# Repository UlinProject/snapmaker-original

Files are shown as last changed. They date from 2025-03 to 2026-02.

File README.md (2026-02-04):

<div id="header" align="center">

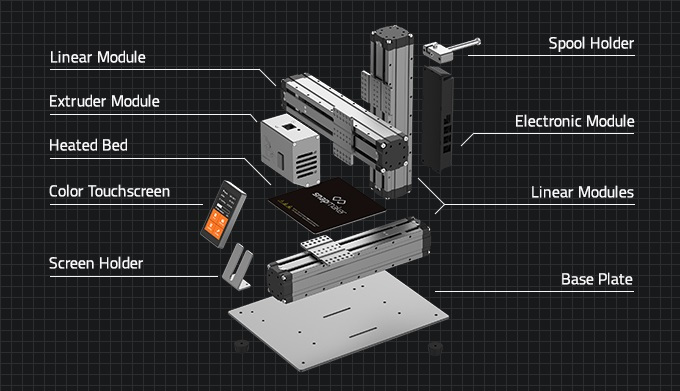
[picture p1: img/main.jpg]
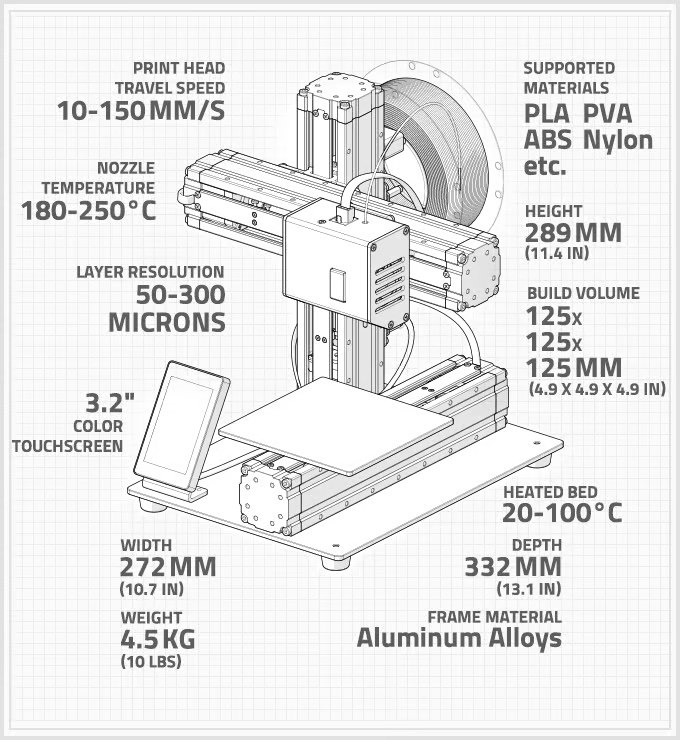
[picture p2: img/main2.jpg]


  <b>[snapmaker-original]</b>
  
  (Information about this 3D printer (Snapmaker original), set of modifications)
  </br></br>
<div id="badges">
  <a href="https://github.com/denisandroid">
    uproject
  </a>
</div>
</div>

## Description
I have been developing devices similar to 3D printers for a long time, I even created one self-assembling Cartesian printer based on a klipper (stm32f407, rails, belts) practically from scratch and one fine day, while studying a local trading platform, I came across this small and interesting printer. Initially, I was not interested in the quality of its 3D printing (I thought that if it prints, then it is already good), and I was only interested in its CNC capabilities and 3 in 1 technologies (3D, CNC, LASER).

My specific printer was manufactured in 2020-2021, and the printer model itself was first manufactured even earlier, around 2017-2018.

## Disclaimer
| :boom: Disclaimer |
|:------------------|
| :warning: Snapmaker is a registered trademark. The author has no affiliation with Snapmaker and does not provide hardware advice. For official support, please refer to the contacts listed on snapmaker. |
| :warning: Your actions and the information described here are entirely at your own risk. The author is not responsible for any damage to your devices. |
| :warning: All information provided is based on personal research and may contain errors. |
| :warning: This material is for informational purposes only. |

## Specifications

### Technique

#### Brain

| name | value |
| ---- | ----- |
| cpu | gd32f105rc6 (ARM; Flash: 256kB; 72-108MHz; external 16Mhz clock; SRAM: 96kB) |
| feedback | usb: ch340g (only 115200 baudrate, or 250000_baudrate/500000_baudrate in custom firmware, stable 921600 baudrate!) |
| power unit | 24V 5A (120w) |
| factory firmware | own firmware 2.11 based on marlin 1.1.0-RC6 (2016-04-24 12:00), gcode: marlin 1.1.0 + own set of instructions, licensed under <a href="https://www.gnu.org/licenses/gpl-3.0.ru.html">GPLv3</a> |
| firmware | ... <a href="./firmware/README.md">See all</a> |
| stepper motors | extruder Unknown 42HD4414-07 (1.8°(200), 2020/08/19) from mocotech, X Unknown 42HD4428-06 (1.8°(200), 2020/09/03) from mocotech, Y Unknown 42HD4428-06 (1.8°(200), 2020/09/03) from mocotech, Z Unknown 42HD4428-06 (1.8°(200), 2020/09/03) from mocotech ... <a href="./mods/BrainVoltageMod.md">See BrainVoltageMod</a> |
| drivers | extruder-rj45 (a4988, 16 steps, ~0.44vref, ~0.56A), X (a4988, 16 steps, ~0.87vref, ~1A), Y (a4988, 16 steps, ~0.87vref, ~1A), Z1 (a4988, 16 steps, ~0.87vref, ~1A), Z2 (X (a4988, 16 steps, ~0.87vref, ~1A)|

About factory firmware: The processor's performance fully covers the printer's capabilities, but the feedback significantly limits it due to the standard data transfer rate of 115200 baud. This is the first printer I know that prints better from a USB flash drive.

#### Factory Firmware Values and Limitations

| name | value |
| ---- | ----- |
| steps per unit | X 400.00, Y 400.00, Z400.00, E92.60 |
| microsteps | 16 |
| maximum feedrates (mm/s) | X 300.00, Y 300.00, Z 5.00, E 25.00 |
| 3d maximum acceleration (mm/s2) | X 1000, Y 1000, Z 100, E 10000 |
| cnc maximum acceleration (mm/s2) | X 100, Y 100, Z 100, E 100 |
| laser maximum acceleration (mm/s2) | X 3600, Y 3600, Z 3600 |
| accelerations printing | 1000.00 |
| accelerations retract | 1000.00 |
| accelerations travel| 1000.00 |
| min feedrate (mm/s) | S0 |
| min travel feedrate (mm/s) | T0 |
| minimum segment time (ms) | B20000 |
| maximum XY jerk (mm/s) | X20.00 |
| maximum Z jerk (mm/s) | Z0.40 |
| maximum E jerk (mm/s) | E5.00 |
| 3d work area | 125x125x125 mm |
| laser work area | 125x125 mm |
| cnc work area | 90x90x50 mm |

The printer manufacturer recommends a default head movement speed of 100 mm/s during printing, and a print speed of 40/50/60 mm/s and a retraction speed of 60 mm/s (at a distance of 5 mm).

The printer has one bad feature in the factory firmware, namely if you forgot to move the carriage home after printing, and it is in the maximum position (and after printing it is always in the maximum position), then after turning the printer off and on and pressing the home button, you will get a short-term impact of the head on the Z-axis limiter. The impact itself on the Z-axis limiter is not very critical, but very unpleasant and can lead to self-unscrewing.

### Physical
A thick aluminum plate on which the modular guides are located. The modular guides are based on a stepper motor + rigid coupling + four-way trapezoidal shaft, on top of the guide there is a thin aluminum plate with a conventional limit switch. The guides used are absolutely identical to the guides along the X, Y, Z axes, the order of connection to the motherboard determines the belonging of the guide to the desired axis. The moving carriage is held by openbuilds rollers.

<b>An anti-play system is present on each axle; the anti-play system operates on the basis of a classic spring.</b>
<b>If you are planning to modify the axes, I recommend starting with the Z-axis thrust bearing (F5-12M 5x12x4), as this is a high-load axis.</b>

#### Accuracy
The design features of the printer and the trapezoid shaft in the guides in combination with the "oak" a4988 should have shown good results, the manufacturer himself assures the accuracy of 50-300 microns. I calibrate each thread for accuracy and enter the data into the slicer, measuring with a caliper with a resolution of 0.01 mm and an error of 0.02 mm. In general, I get:

| NAME | PETG (default firmware)  | PLA (default firmware)  | PLA(klipper firmware +pa+is) |
| --- | --- | --- | --- |
| min absolute deviation (X and Y axes) | ~0.02mm | ~0.02mm | ~0.01mm |
| average absolute deviation (X and Y axes) | ~0.08mm | ~0.12mm | ~0.07mm |
| max absolute deviation (X and Y axes) | ~0.17mm | ~0.20mm | ~0.09mm |

In general, I have summarized many results of different filaments under the general one and described the general deviation of the two axes. I would also like to note that this printer gives more accurate results on the X-axis than on the Y-axis.

<b>The section is not finished yet.</b>

#### Cooling
Almost all of them use 24V fans, connected directly to 24V, i.e. they are uncontrollable. All fans are absolutely tiny and create a lot of noise, the saddest thing is that they are not very productive and I once managed to catch a traffic jam in the extruder due to not very good weather conditions.

It is recommended to replace almost all fans with larger ones.

#### Display
A very good solution, you can just take it as a phone and control the printer, a display with good resolution and more or less high-quality color gamut, not requiring a stylus. The solution is a ready-made purchased uart solution with its own microcontroller and program. The display is poorly compatible with the standard gcode for text displays and, for example, does not allow much under octoprint. I repeat that this display does not receive an image from the main microcontroller, but is independent.

### 3 In one

#### Extruder (3D)
A classic extruder built on the basis of an unknown to me full-size nemo 17 (1.8°(200), 42HD4414-07, 2020/08/19) from mocotech and gears (1:1, factory e-steps 92.60), a radiator noticeably larger than its classic versions, a convenient unknown to me thermal barrier, which involves fastening by screwing in one countersunk screw. By selection, it was established that the heating block itself is E3D V5, but with an unknown to me thermal barrier, which does not imply unscrewing from the block.

##### Bad design #1 (3D)
Instead of a capsule thermistor, a "droplet" type is used; the sensor itself is simply suspended inside the heating block and can move freely within it.

##### Bad design #2 (3D)
The manufacturer has provided a way to easily remove the cover and unscrew the fuser unit, but the rigid heating wires make it somewhat difficult to remove. Furthermore, if the "plastic plug" accidentally gets into the extruder during printing, the entire print head must be disassembled, a very time-consuming and tedious task.

##### Bad design #3 (3D)
The heating block itself is not insulated and, combined with an ineffective PID controller, the temperature fluctuates constantly.

##### Bad design #4 (3D)
While twisted pair cable is certainly an interesting and attractive solution when combined with a classic RJ45 connector, the cable cross-section from the "brain" to the extruder head proved unsatisfactory. Significant heating was observed, and the cable at best delivers 1.49 A with a voltage drop of 1.5 V (using an extruder with an output power of ~40 W will only deliver ~35 W, and even then, the resistance will fluctuate as the heater heats up. Using more powerful heaters of 50-60-80 W is impossible. Switching to an external MOSFET with a higher-quality cable resulted in a voltage drop of 0.1-0.2 V and an output power of approximately ~38 W using the same heater block, as well as the possibility of using more powerful extruders).

#### Bed (3D)
The textolite is small in size (128x128 mm), heating is exclusively resistive (24V, did not determine the power), heating up to 60-65 degrees is preferable (It is believed that temperatures above 80 degrees can damage the sticker coating). The main disadvantage of this table is the lack of insulation and all the heat is directed both to the platform itself and to heating its base (guide). Also, the bolts for fastening the platform to the guide are slightly larger than required, because of this, the screws themselves cut into the sticker glued to the platform a little (it is recommended to simply add a washer between the screw and the carriage, and then the screw will never damage the coating.). Another plus is that this sticker does not require any glue at all when printing PLA / PETG.

The first layer is calibrated in the printer very poorly, the calibration of the first layer is more truthful only at the moments of full heating of the platform, which the manufacturer did not provide for in the firmware. After calibrating the surface, you can more clearly evaluate the first layer on the model https://www.thingiverse.com/thing:3797458 (I am not the author of this model, it is simply in the public domain, <a href="https://creativecommons.org/licenses/by-nc/4.0/">Creative Commons - Attribution - Non-Commercial license</a>), and then perform the final calibration based on the model.

#### Spindle (CNC)
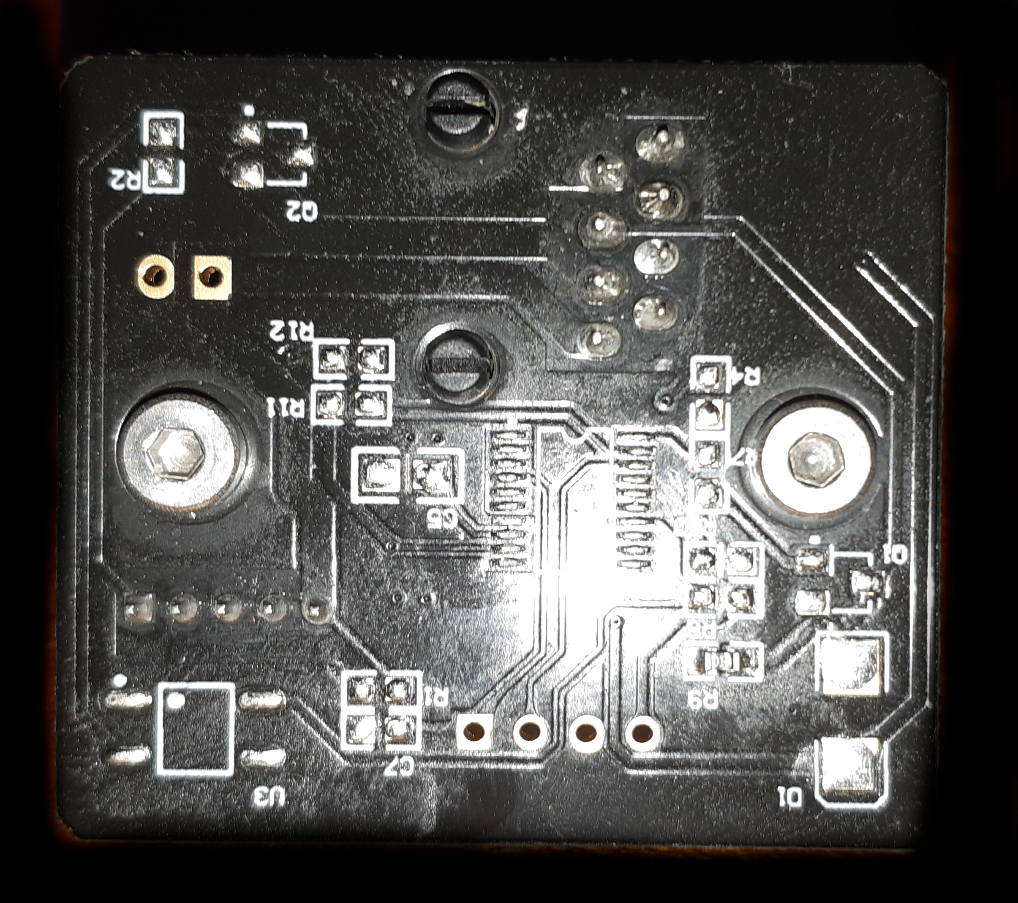
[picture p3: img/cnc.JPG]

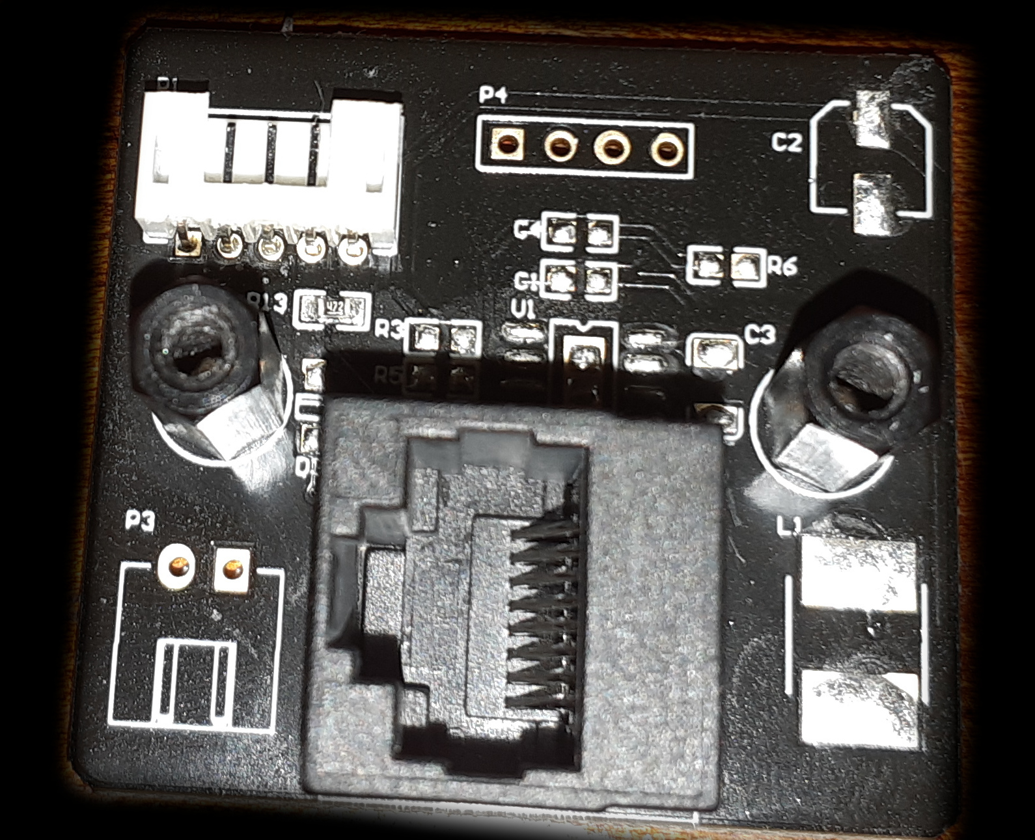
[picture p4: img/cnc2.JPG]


Uses a weak spindle 30W RBI-365024 24V, the main software assumes the use and configuration of specific cutters, the ability to perform drilling was not found. There are many shortcomings, no automatic centering, no speed control, a lot of noise during operation. The spindle control board is supposedly designed for control, but in the copy that I had, the board actually consisted of two resistors that do not assume speed control, there is only on / off control, carried out by the main brain board.

Also one of the minuses - the fastening of cutters / drills is not very good.

The spindle itself consists of a BLDC DC motor, MOSFET transistors, and a 4931ET driver (the electronics are hidden inside the spindle). The following pins are used for connection: AR, FG, FR, PWM, GND, and VCC (interestingly, there is a thick layer of solder between the PWM and GND pins from the factory).

#### Laser
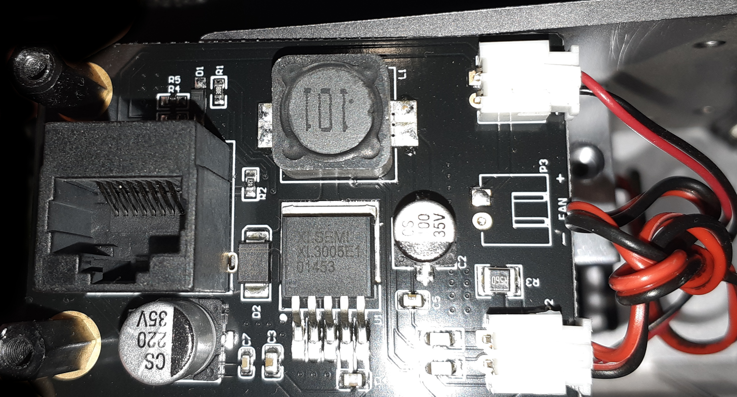
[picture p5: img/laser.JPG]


I have hardly used it and have not tested it. There is a dc/dc converter board inside and presumably the feedback and dc/dc regulation works. (will be added).

### Mods

#### Cooling of the thread (3D)
Cooling of the filament during printing is arranged in the strangest way, in general it is enough for someone, but for beginners I recommend printing and using https://www.thingiverse.com/thing:3403426 (I am not the author of this model, it is simply in the public domain, <a href="https://creativecommons.org/licenses/by/4.0/">Creative Commons - Attribution license</a>.)

#### Spool holder (3D)
<a href="./mods/SpoolHolder.md">See</a>

#### Thread Spool Holder (3D)
The thread holder allows you to correctly position the thread flow at a certain height, together with the modification of the holder, this is a comprehensive solution. Also, one of the advantages of this holder is that it allows you to easily move the engine control screen to the very top. https://www.thingiverse.com/thing:2757715 (I am not the author of this model, it is simply in the public domain, <a href="https://creativecommons.org/licenses/by/4.0/">Creative Commons - Attribution license</a>.)

#### Power unit
<a href="./mods/PowerUnit.md">See</a>

#### Strange Y-axis settings (settings for factory firmware only)
Initially, one oddity was noticed in the printer: if the X and Z axes were correctly limited by software and did not reach the limit, then the Y axis at the possible maximum slightly crashed into an obstacle. In general, this is not critical, since it crashed only one step and there is such a possibility that this is only me, but here is the fix:

```gcode
M1025 X131.00 Y128.00 Z128.00
M500
```
This g-code will determine the maximums for the axes and save the changes.

#### Brain cooling (cooling)
<a href="./mods/BrainCooling.md">See</a>

#### Octoprint (3D)
<a href="./mods/BrainCooling.md">See</a>

#### UART (feedback)
<a href="./mods/Uart.md">See</a>

#### Volcano (3D)
<a href="./mods/Volcano.md">See</a>

#### Gaps in the guides
The Y-guide design is not very good and involves large gaps through which debris can get in and affect the trapezoid screws; from time to time, various debris can get in there, including bolts or nuts (which, by the way, once happened to me), and especially considering that the manufacturer also assumes milling on this printer, the issue of debris is very acute.

There was a solution on the Internet using a paper accordion filter, which in theory can be made by yourself and the necessary parts can be printed for it https://www.thingiverse.com/thing:2828419 (I am not the author of this model, it is simply in the public domain, <a href="https://creativecommons.org/licenses/by-nc/4.0/">Creative Commons - Attribution - Non-Commercial license</a>.), at the moment I have not used this modification.

#### TMC2209? (stepper motor drivers)
In general, it would be possible to simply desolder the a4988 with a hair dryer and replace them with tmc2209, since they have similar pinout, and also change the harness a little and maybe even run the setup via uart and sensorless pointing, but at the moment I decided not to do this. The reason for using tmc2209 is simple, it is the ability to greatly reduce the noise of the stepper motors, but the StealthChop algorithm can also cause problems with circular geometry, and because of the a4988, the stepper motors are very noisy even in standby mode.

#### Klipper (new firmware)
Yes, this printer and this motherboard can be updated with Klipper, you can find the firmware in the firmwares called Klipper, you can simply follow the instructions and update the firmware without using JTAG or other means, just drop the file on a flash drive. Future updates of Klipper can be just as easy, also you can revert to the factory firmware at any time or to any other firmware.

| name | version | mcu | rate |
| ---- | ----- | ----- | ----- |
| Klipper_6_2025Demo460800.Bin | 121 commands, v0.12.0-452-g75a10bfca-dirty-20250308_020116-r510 / gcc: (Arch Repository) 14.2.0 binutils: (GNU Binutils) 2.43) | GD32F105RC6 | uart 480600 baudrate |

<a href="./firmware/Klipper.md">See</a>

#### Resonance compensation (only for klipper firmware)
<a href="./resonances/Readme.md">See</a>

#### Cura (slicer)
<a href="./cura/Readme.md">See</a>

#### My configuration (2025)

| name | value |
| ---- | ----- |
| heat block | volcano Plated Copper with insulator (TriangleLab) |
| heater | 24V 40W (TriangleLab), factory power limitation for the wires is approximately ~35W |
| sensor | 104NT-4 R025H42G in the sleeve (TriangleLab) |
| nozzle | E3D Volcano 0.4 (TriangleLab) |
| thermal barrier | unknown (the factory hole diameter was used, the thread was cut without additional drilling, and the heat break was simply selected and is unknown to me (the modifications to the heatsink suggest compatibility with factory heat breaks)). |
| lighting | ws2812b ribbon (5V, RP2040) |
| fan | 50mmX50mm 12V extruder (always on), DEFAULT CONFIGURATION |
| extruder | default Unknown 42HD4414-07 (~0.5A), MK8 (30 TEETH) |
| firmware | brain: klipper (v0.12.0, UART 921600baudrate), rp2040: klipper (v0.12.0, USB) |

#### My configuration (2026)

| name | value |
| ---- | ----- |
| heat block | volcano Plated Copper with insulator (TriangleLab) |
| heater | 24V 40W (TriangleLab), external MOSFET LR7843+new_wiring (support: 40,50,60,80..~120W) |
| sensor | 104NT-4 R025H42G in the sleeve (TriangleLab) |
| nozzle | E3D Volcano 0.4 (TriangleLab) |
| thermal barrier | titanium V6 (TriangleLab) (the heatsink was drilled out to a new, larger diameter, a new thread was cut, and an additional hole was made in the heatsink for installing another mounting screw for the heat break.) |
| wiring | general protection of all grounded wires, general grounding |
| lighting | ws2812b ribbon (5V, RP2040) |
| fan | 50x50mm 12V cooling extruder (only ON/OFF, always enabled by default if there is no control from the MCU, dc-dc LM2596S, PCA9685+LinuxMcu), default print_fan 24V (PWM 0-100%, module mosfet LR7843, PCA9685+LinuxMcu), 80x80mm 5V power unit (only ON/OFF, always enabled by default if there is no control from the MCU, dc-dc LM2596S, PCA9685+LinuxMcu+DS18B20), 80x80mm brain 5V cooling fan (PWM 0-100%, module mosfet LR7843, PCA9685+LinuxMcu+GD32F105InternalADCSensor)|
| extruder | new 17HS4401S (0.9°, configured ~1.34А), MK8 (50 TEETH) + THRUST BEARING (F5-12M 5x12x4) |
| axis | modified with thrust (F5-12M 5x12x4) bearing, new graphite screw nuts (T8x2x8, all axles) |
| firmware | klipper (v0.13.0, UART 460800baudrate), rp2040: klipper (v0.13.0, USB), linux_mcu: klipper (v0.13.0, internal process) |

## General impressions
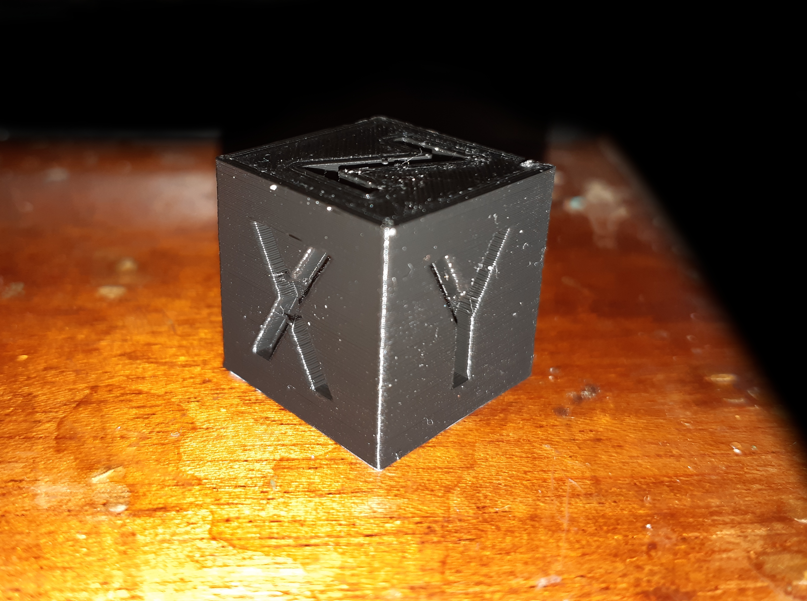
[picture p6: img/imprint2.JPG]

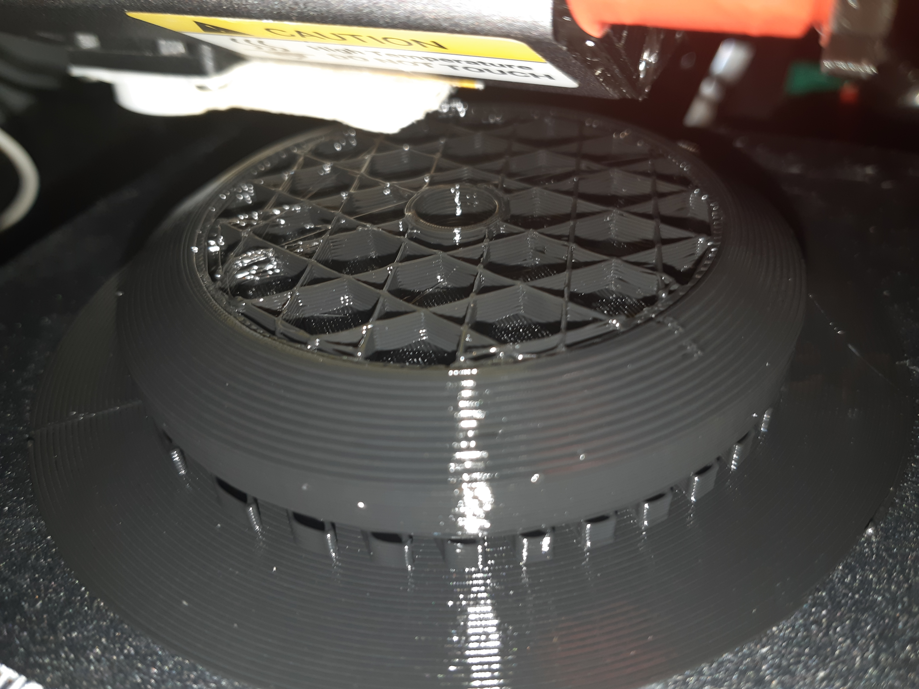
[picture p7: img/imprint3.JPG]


I liked the printer first of all for its assembly, it is completely aluminum, there are very few plastic parts, the printer creators even used thread locks and the idea of 3 in one is very catchy, but it has a very strong drawback, namely NOISE, which can be reduced by modifying the fans and ultimately the drivers, spindle...

As for the price, it turned out that this printer did not cost me that much, since the authors cut it out of their line, but at the same time, if I needed 3D printing, I could have initially bought something similar fast on "klipper".

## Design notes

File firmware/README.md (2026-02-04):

## Disclaimer
The firmware presented here is provided as is, I am not responsible for your damaged devices. All information described here is solely my experience and can be both useful and harmful to the end user. You can reflash your printers only at your own risk. Damage to your device can occur at any stage of the end user's actions. All images and firmware presented here are the property of their authors.

Snapmaker is a registered trademark, to which I have no relation, you can always contact the official contacts listed on the website snapmaker.com. All rights reserved.

## Firmware

| name | value | mod_list | stable |
| ---- | ----- | ----- | ----- |
| 32Base-2_11Original.Bin | The latest current firmware from the manufacturer in 2019, downloaded from open sources. Licensed under <a href="https://www.gnu.org/licenses/gpl-3.0.en.html">GPLv3</a> | | + |
| 32Base_2_11_01Demo250000BOUD.Bin | The first experiment on modifying this firmware, testing the reflashing method. Licensed under <a href="https://www.gnu.org/licenses/gpl-3.0.en.html">GPLv3</a> | +uart 115200BAUDRATE -> 250000BAUDRATE; | +(only tests) |
| 32Base_2_11_02Demo500000BOUDAndAdvancedOK | Second experiment, 500000BAUDRATE and ADVANCED_OK tests. | +uart 115200BAUDRATE -> 500000BAUDRATE; +uart advanced_ok; | +(only tests) |
| 32Base_2_11_04Demo500000BOUDAndMoreSerialMods | Experimenting with using the recommended settings for OctoPrint. Licensed under <a href="https://www.gnu.org/licenses/gpl-3.0.en.html">GPLv3</a> | +uart 115200BAUDRATE -> 500000BAUDRATE; +uart advanced_ok; +fix: BLOCK_BUFFER_SIZE(8->64); +fix: BUFSIZE(8->32); +fix: RX_BUFFER_SIZE(512->2048); | +(only tests) |
| Klipper | <a href="./Klipper.md">See</a> | ... | +(only tests) |

## Is it possible to get a brick when flashing?
Very low probability, since you can flash any firmware at any time, also remember that I am not responsible for your actions, you can use these firmwares only at your own risk.

## Saving settings?
Any firmware change resets the default settings, constantly having to adjust the height of the card.

## How to reflash?
1. Copy any file and rename it to Update.Bin to a USB disk formatted in Fat32.
2. Turn off the printer and insert the USB disk into the USB port.
3. Turn on the printer. If the LED changes as below, the update is successful.
- The blue LED blinks slowly for about 5 seconds.
- Then the LED turns off for about 2 seconds.
- The LED starts blinking quickly.
4. The flashing process is complete.

## Machine resonances?
<a href="./../resonances/Readme.md">See</a>

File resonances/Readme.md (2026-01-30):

#### Resonance compensation (only for klipper firmware)

## Description
It seems that this is exactly what this printer lacked from the factory. The printer itself has very good indicators on the X axis from the factory, but with the Y axis, not everything is so good even according to accuracy tests, after this calibration, the printer accuracy has increased significantly and it became possible to increase the acceleration, as well as print at higher speeds. I do not recommend making such accelerations as recommended by autocalibration, start from the fact that the acceleration from the factory is 1500 (on printing) / 3000 (on the laser), you can use 3000/6000 on printing, and maybe more, but I do not recommend you to set 76800/61500 right away, this is too much, remember that due to the features of the printer (trapezoidal shafts) the printer is subject to strong friction, you can thus wear out this printer very quickly, and I also recommend that you lubricate it more often.

<b>Please note that polyoxymethylene (POM) nuts are officially considered lubrication-free; they operate on the dry lubrication principle, and lubrication will only increase dust adhesion. However, lubrication has been proven to reduce friction even on POM nuts, and I use specialized lubricants that reduce dust adhesion. Your choice should be based solely on your own needs.</b>

<details>
  <summary>## My results (2025, Demo01, standard configuration, X-(mzv, vibrations = 0.0%, smoothing ~= 0.017, max_accel <= 45000 mm/sec), Y-(3hump_ei, vibrations = 3.7%, smoothing ~= 0.050, max_accel <= 12600 mm/sec))</summary>
    
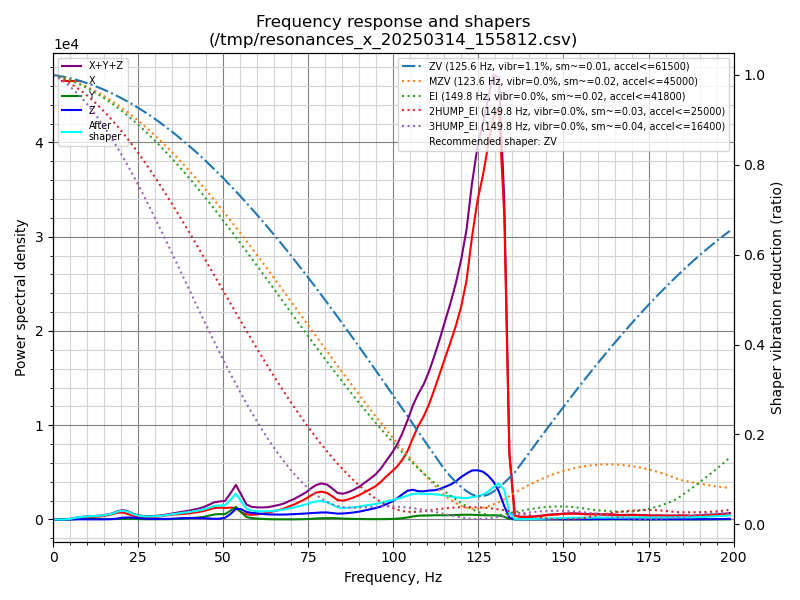
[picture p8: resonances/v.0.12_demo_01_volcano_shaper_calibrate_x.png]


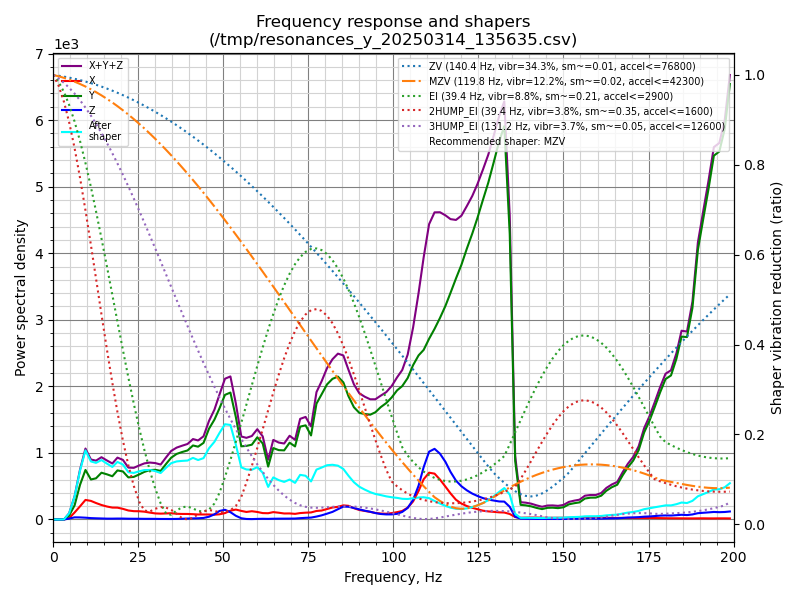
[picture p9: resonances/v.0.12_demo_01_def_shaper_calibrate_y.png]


X:
```
Fitted shaper 'zv' frequency = 125.6 Hz (vibrations = 1.1%, smoothing ~= 0.015)
To avoid too much smoothing with 'zv', suggested max_accel <= 61500 mm/sec^2
Fitted shaper 'ei' frequency = 149.8 Hz (vibrations = 0.0%, smoothing ~= 0.018)
To avoid too much smoothing with 'ei', suggested max_accel <= 41800 mm/sec^2
Fitted shaper '2hump_ei' frequency = 149.8 Hz (vibrations = 0.0%, smoothing ~= 0.028)
To avoid too much smoothing with '2hump_ei', suggested max_accel <= 25000 mm/sec^2
Fitted shaper '3hump_ei' frequency = 149.8 Hz (vibrations = 0.0%, smoothing ~= 0.040)
To avoid too much smoothing with '3hump_ei', suggested max_accel <= 16400 mm/sec^2
Fitted shaper 'mzv' frequency = 123.6 Hz (vibrations = 0.0%, smoothing ~= 0.017)
To avoid too much smoothing with 'mzv', suggested max_accel <= 45000 mm/sec
```

Y:
```
Fitted shaper 'zv' frequency = 140.4 Hz (vibrations = 34.3%, smoothing ~= 0.013)
To avoid too much smoothing with 'zv', suggested max_accel <= 76800 mm/sec^2
Fitted shaper 'mzv' frequency = 119.8 Hz (vibrations = 12.2%, smoothing ~= 0.018)
To avoid too much smoothing with 'mzv', suggested max_accel <= 42300 mm/sec^2
Fitted shaper 'ei' frequency = 39.4 Hz (vibrations = 8.8%, smoothing ~= 0.208)
To avoid too much smoothing with 'ei', suggested max_accel <= 2900 mm/sec^2
Fitted shaper '2hump_ei' frequency = 39.4 Hz (vibrations = 3.8%, smoothing ~= 0.348)
To avoid too much smoothing with '2hump_ei', suggested max_accel <= 1600 mm/sec^2
Fitted shaper '3hump_ei' frequency = 131.2 Hz (vibrations = 3.7%, smoothing ~= 0.050)
To avoid too much smoothing with '3hump_ei', suggested max_accel <= 12600 mm/sec
```

The results are more like the truth, but I'm not entirely sure about them, since these are the very first resonance measurements I made on this printer. The measurement was made directly on the nozzle itself, and on the heated platform at its very edge. What I can say is that the autocalibrator's choice of 1.1% vibrations is very strange, when you can choose 0%, but not at such high accelerations, and I also can't say with certainty that the chosen shaper will help 100%, since there are spikes at different frequencies.

## At the moment I am using this configuration (Demo01)

```toml
[input_shaper]
shaper_type_x: mzv
shaper_freq_x: 123.6
shaper_type_y: 3hump_ei
shaper_freq_y: 131.2
```

Yes, the Y axis is limited to a max of 12600 acceleration, but that seems to be the best the shaper can offer on that axis with minimal vibration.
  
</details>

<details open>
  <summary>## My results (2026, design changes, X-(mzv, vibrations = 0.0%, smoothing ~= 0.014, max_accel <= 49800 mm/sec), Y-(2hump_ei, vibrations = 1.0%, smoothing ~= 0.031, max_accel <= 20200 mm/sec))</summary>
    
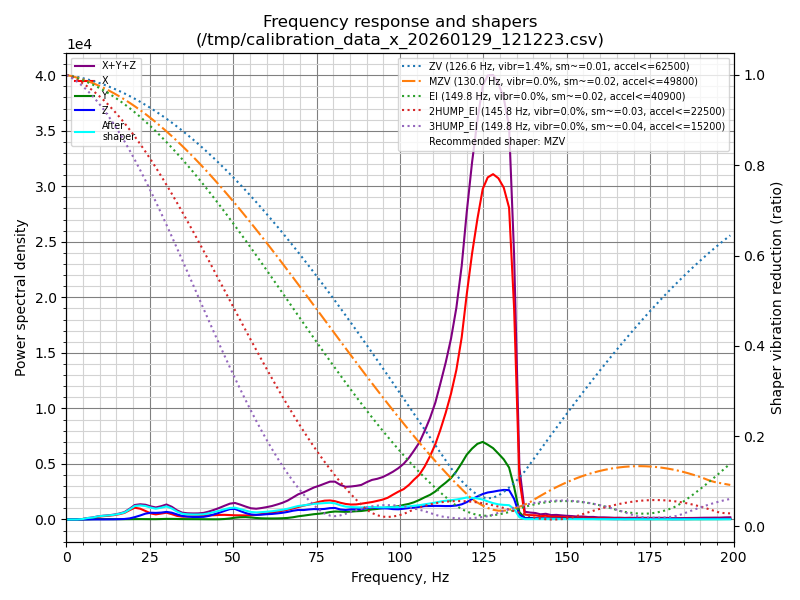
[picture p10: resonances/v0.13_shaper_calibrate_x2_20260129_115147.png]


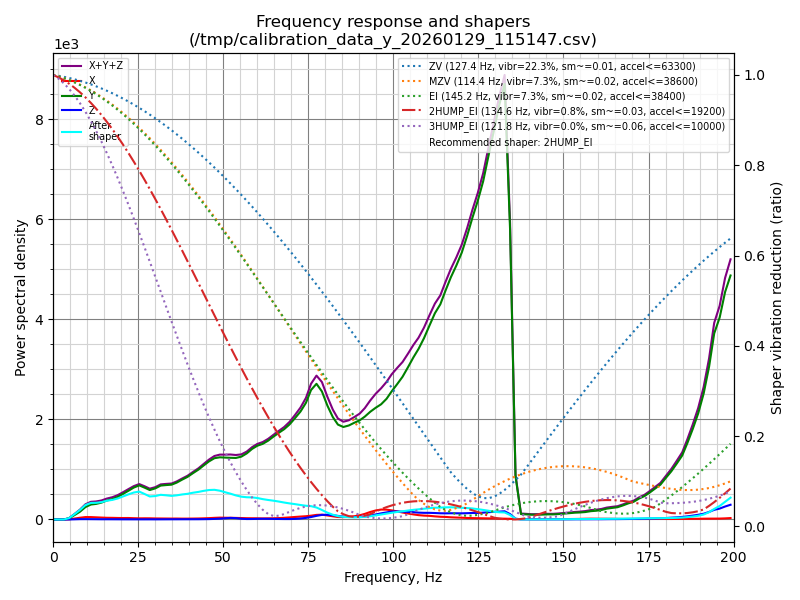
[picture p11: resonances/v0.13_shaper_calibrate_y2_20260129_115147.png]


X:
```
// Fitted shaper 'zv' frequency = 126.6 Hz (vibrations = 1.4%, smoothing ~= 0.013)1
// To avoid too much smoothing with 'zv', suggested max_accel <= 62500 mm/sec
// Fitted shaper 'mzv' frequency = 130.0 Hz (vibrations = 0.0%, smoothing ~= 0.014)
// To avoid too much smoothing with 'mzv', suggested max_accel <= 49800 mm/sec
// Fitted shaper 'ei' frequency = 149.8 Hz (vibrations = 0.0%, smoothing ~= 0.016)
// To avoid too much smoothing with 'ei', suggested max_accel <= 40900 mm/sec
// Fitted shaper '2hump_ei' frequency = 145.6 Hz (vibrations = 0.0%, smoothing ~= 0.028)
// To avoid too much smoothing with '2hump_ei', suggested max_accel <= 22500 mm/sec
// Fitted shaper '3hump_ei' frequency = 149.8 Hz (vibrations = 0.0%, smoothing ~= 0.040)
// To avoid too much smoothing with '3hump_ei', suggested max_accel <= 15200 mm/sec

// Recommended shaper_type_x = mzv, shaper_freq_x = 130.0 Hz
// shaper_type_x:mzv shaper_freq_x:130.000 damping_ratio_x:0.100000
// shaper_type_y:2hump_ei shaper_freq_y:138.200 damping_ratio_y:0.100000
// Shaper calibration data written to /tmp/calibration_data_x_20260129_121223.csv file
```

Y:
```
// Fitted shaper 'zv' frequency = 129.2 Hz (vibrations = 24.8%, smoothing ~= 0.013
// To avoid too much smoothing with 'zv', suggested max_accel <= 65100 mm/sec
// Fitted shaper 'mzv' frequency = 115.6 Hz (vibrations = 7.0%, smoothing ~= 0.017)
// To avoid too much smoothing with 'mzv', suggested max_accel <= 39400 mm/sec
// Fitted shaper 'ei' frequency = 149.8 Hz (vibrations = 7.9%, smoothing ~= 0.016)
// To avoid too much smoothing with 'ei', suggested max_accel <= 40900 mm/sec
// Fitted shaper '2hump_ei' frequency = 138.2 Hz (vibrations = 1.0%, smoothing ~= 0.031)
// To avoid too much smoothing with '2hump_ei', suggested max_accel <= 20200 mm/sec
// Fitted shaper '3hump_ei' frequency = 125.0 Hz (vibrations = 0.0%, smoothing ~= 0.057)
// To avoid too much smoothing with '3hump_ei', suggested max_accel <= 10600 mm/sec

// Recommended shaper_type_y = 2hump_ei, shaper_freq_y = 138.2 Hz
// shaper_type_x:mzv shaper_freq_x:123.600 damping_ratio_x:0.100000
// shaper_type_y:2hump_ei shaper_freq_y:138.200 damping_ratio_y:0.100000
// Shaper calibration data written to /tmp/calibration_data_y_20260129_115147.csv file
```

As paradoxical as it may sound, testing shows that after a year of active use, the printer has become even more rigid and can now handle even higher accelerations than before. But there's nothing unusual about it; I simply performed this second calibration after a complete teardown, high-quality lubrication, and the installation of new black POM nuts, along with my own modification—installing thrust bearings on the stepper motors (which only works effectively on the Z-axes).

```toml
[input_shaper]
shaper_type_x: mzv
shaper_freq_x: 130.0
shaper_type_y: 2hump_ei
shaper_freq_y: 138.2
```

</details>

## How to calibrate?
There are no special recommendations here, I recommend using the official documentation, I will simply tell you how I calibrated this printer. For starters, you can use any high-speed microcontroller, for example, rp2040/rp2350 with an adxl345 accelerometer, I simply used stm32f103 with an adxl345 accelerometer soldered in by myself and flashed it with the latest klipper firmware, one microcontroller with adxl is enough for separate calibration of one axis, and then another, just calibrate one axis and move the calibrator to the other, and then calibrate it too.

### Configuration example
Note the order of the X, Y, Z axes and determine in which axis order you install the accelerometer.
```toml
[mcu mcu2]
serial: /dev/serial/by-id/usb-Klipper_stm32f103xe_25002700010000343333574E-if00
restart_method: command

[adxl345 AXES_X_OR_Y]
cs_pin: mcu2:PA4
spi_speed: 5000000
# axes_map: y, x, z # Change only if you think it is necessary to ensure that the axes match.
spi_bus: spi1
rate: 3200

[resonance_tester]
accel_chip: adxl345 AXES_X_OR_Y
move_speed: 60
probe_points:
    62.5, 62.5, 20

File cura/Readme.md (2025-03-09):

#### Cura
In general, you can use Luban, it has good settings for this printer on the old Cura engine, but it has a simpler setup interface and in some places even more thought out than Cura, but very limited in functionality. Or a completely different slicer, but I adapted specifically Cura.

| name | value |
| ---- | ----- |
| X (width) | 125.0 |
| Y (width) | 125.0 |
| Z (height) | 125.0 |
| Build plate shape | Rectangler |
| Origin at center |  |
| Heated bed | + |
| Heated build volume |  |
| G-code flavor | Marlin |
| X min | -20 |
| Y min | -10 |
| X max | 10 |
| Y max | 10 |
| Gantry Height | 125.0 |
| Number of Extruders | 1 |
| Apply Extruder offsets to gcode | + |

Start G-code
```gcode
M1005

T0
M82 ;absolute extrusion mode
;Start GCode begin
M104 S{material_print_temperature_layer_0} ;Set Hotend Temperature
M140 S{material_bed_temperature_layer_0} ;Set Bed Temperature
G28 ;home
M400 ; WAIT END G0/G1
M109 S{material_print_temperature_layer_0} ;Wait for Hotend Temperature
M190 S{material_bed_temperature_layer_0} ;Wait for Bed Temperature
G90 ;absolute positioning
G0 X-10 Y-10 F3000
G0 Z0 F1800
G92 E0
G1 E25 F190 ; Extrusion
G92 E0

G0 X0 Y0 F3000 ;Move to origin
G0 Z1 F1800 ;Move up to avoid scraping against heated bed

;Start GCode end
```

End G-code
```gcode
M140 S0
M107
;End GCode begin
M400 ; WAIT END G0/G1
M104 S0 ;extruder heater off
M140 S0 ;heated bed heater off (if you have it)
G90 ;absolute positioning
G92 E0
G1 E-1 F300 ;retract the filament a bit before lifting the nozzle, to release some of the pressure
G1 Z125 E-1 F3000 ;move Z up a bit and retract filament even more
G1 X0 F3000 ;move X to min endstops, so the head is out of the way
G1 Y125 F3000 ;so the head is out of the way and Plate is moved forward
;End GCode end
M82 ;absolute extrusion mode
M104 S0
;End of Gcode
```

| name | value |
| ---- | ----- |
| Nozzle size | 0.4 |
| Compatible material diametr | 1.75 |
| Nozzle offset X | 0.0 |
| Nozzle offset Y | 0.0 |
| Cooling Fan Number | 0.0 |
| Extruder Start G-code duration | 0.0 |
| Extruder End G-code duration | 0.0 |

Next, I recommend installing `Cura-MaterialSettingsPlugin` or a similar plugin to distribute settings between the filament and the printer profile.

In the files I will attach a print profile adapted for this printer (but I have a "volcano") and an example of settings for one of the types of plastic.

<b>The section is not finished yet.</b>

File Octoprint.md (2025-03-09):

#### Octoprint


I have long been accustomed to the "klipper" and at the moment I wanted to keep the original brains, but at the same time have the ability to print and control the printer over the network, the simplest solution was to install an octoprint.

There are no special recommendations here, and some parameters may not suit you. (there may also be errors here)

| name | value |
| ---- | ----- |
| name | Snapmaker Original |
| model | Snapmaker Original |
| form factor | Rectangler |
| origin | Lower left |
| heated bed | + |
| width (X) | 125 |
| depth (Y) | 125 |
| height (Z) | 125 |
| axes X | 10000 |
| axes Y | 10000 |
| axes Z | 220 |
| axes E | 1000 |
| nozzle diameter | 0.4 |
| number of extruders | 1 |
| default extrusion length | 5 |

<b>Please note</b> that if you are using 500000 baud, this needs to be specified in the Octoprint alternative speeds, but if you are using 250000 baud, nothing like that is required.

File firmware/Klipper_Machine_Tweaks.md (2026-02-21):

### Klipper Machine Tweaks

#### # UART Interface
Use the built-in UART interface for direct MCU communication.

Documentation: <a href="../mods/Uart.md#direct-uart-connection-to-sbc-single-board-computer">See Uart.md</a>.

#### # USB (cmdline.txt)
Optimizations for the USB stack and CPU scheduling.

Path (add to the end): /boot/firmware/cmdline.txt
```
 dwc_otg.lpm_enable=0 dwc_otg.fiq_fsm_enable=1 dwc_otg.nak_holdoff=1
```
<b>dwc_otg:</b> Disables USB power management and optimizes interrupt handling to ensure stable MCU connection.

#### # USOLCPUS (cmdline.txt)
Dedicate one CPU core exclusively to running Klipper.

Path (add to the end): /boot/firmware/cmdline.txt
```
 isolcpus=3
```
<b>isolcpus=3:</b> Isolates the 4th CPU core from the Linux general scheduler for exclusive Klipper use.

##### Process Priority & CPU Affinity
Script: /bin/klipper_update_priority
```bash
#! /bin/bash
KLIPPER_PID=$(pgrep -f "klippy.py")

if [ -n "$KLIPPER_PID" ]; then
    chrt -f -p 40 $KLIPPER_PID       # Set Real-Time priority
    taskset -cp 3 $KLIPPER_PID       # Bind to isolated core 3
    ionice -c 1 -n 0 -p $KLIPPER_PID # Maximize I/O priority
fi
```
File: /etc/cron.d/klipper
```
@reboot root bash /bin/klipper_update_priority
*/5 * * * * root bash /bin/klipper_update_priority
```
File: /etc/default/irqbalance
```
IRQBALANCE_BANNED_CPUS=00000008
```

#### # System Performance (/etc/rc.local)

##### CPU Frequency

Script (add to the end): /etc/rc.local
```bash
cpupower frequency-set --min 1.2Ghz
cpupower frequency-set -g performance
```

##### Logging & Network
Script (add to the end): /etc/rc.local
```bash
mount -t tmpfs tmpfs /home/alarm/printer_data/logs/
iw dev wlan0 set power_save off
```

##### Extreme Real-Time Tuning
Note: Use with caution. Removes the 5% CPU safety margin for the OS.

Script (add to the end): /etc/rc.local
```bash
sysctl -w kernel.sched_rt_runtime_us=-1
```

##### CMA (if you don't use the display, rpi3 machine)
Note: Just free up some RAM by cutting cma. How much free space is in the CMA? Check with cat /proc/meminfo (usually free 28m).

Path (add to the end): /boot/firmware/cmdline.txt
```
 cma=32M
```

##### Mitigations + off_audit (be aware of the risks)
Path (add to the end): /boot/firmware/cmdline.txt
```
 mitigations=off audit=0
```

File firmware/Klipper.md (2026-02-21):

## Description
A full featured clipper port for this printer, allowing you to overclock and expand the capabilities ("pressure advance", "input shaper", "bl-touch", "nozzle cleaner", "fan control", ...) of this printer using a single board computer and other additional microcontrollers.

## Disclaimer
The firmware presented here is provided as is, I am not responsible for your damaged devices. All information described here is solely my experience and can be both useful and harmful to the end user. You can reflash your printers only at your own risk. Damage to your device can occur at any stage of the end user's actions. All images and firmware presented here are the property of their authors.

Snapmaker is a registered trademark, to which I have no relation, you can always contact the official contacts listed on the website snapmaker.com. All rights reserved.

## Firmware
| name | value | stable |
| ---- | ----- | ----- |
| Klipper_6_2025Demo460800.Bin | Experimental current (as of 2025) demo firmware klipper. Licensed under <a href="https://www.gnu.org/licenses/gpl-3.0.en.html">GPLv3</a> | +-(only tests) |
| Klipper_10_v0.12.0_2025.zip | Relevant for start 2025, functionality is not cut. Firmware in the archive, you need to unpack and select the desired baudrate, if you do not know the baudrate take 250000, ONLY UART (UART via USB or directly). Licensed under <a href="https://www.gnu.org/licenses/gpl-3.0.en.html">GPLv3</a> | +(only tests) |
| Klipper_12_v0.13.0_2025.zip | Relevant for 2025-2026, functionality is not cut. Firmware in the archive, you need to unpack and select the desired baudrate, if you do not know the baudrate take 250000, ONLY UART (UART via USB or directly). Licensed under <a href="https://www.gnu.org/licenses/gpl-3.0.en.html">GPLv3</a> | + |

## How to reflash?
1. Copy any file and rename it to Update.Bin to a USB disk formatted in Fat32.
2. Turn off the printer and insert the USB disk into the USB port.
3. Turn on the printer. If the LED changes as below, the update is successful.
- The blue LED blinks slowly for about 5 seconds.
- Then the LED turns off for about 2 seconds.
- The LED starts blinking quickly.
4. The flashing process is complete.

## Don't forget to remove the flash drive
The "klipper" firmware does not delete the "Update.Bin" file after flashing, so you can constantly reflash the device when you turn it on (even if you don't want to). It is better to either remove the flash drive or delete the "Update.Bin" file on it. In the Marlin firmware, this is done automatically.

## Is it possible to return to the factory firmware?
At any time, in the same way, by dropping the original Update.bin onto a flash drive.

## 921600/500000/460800/250000?
I can't give you a definitive answer, but this printer works fine at 500,000 baud and above. I currently use 921600 regularly, but Klipper officially recommends 250,000, and according to official statements, that should be enough, but the overall command throughput may be low.

<i>After switching to a detachable UART cable (previously, it was simply soldered on, which was a nuisance), I once experienced an MCU timeout and stopped using the 921600, but the 460800 is quite stable under all conditions.</i>

## Which single board computer to use?
This printer is not demanding on the performance of the single board computer, but it is recommended to take a single board computer not lower than the Raspberry pi 3, Raspberry pi 4/5, and zero 2w versions (be careful with the zero versions, you only have 512 MB of RAM or even less because of the graphics processor, this can greatly limit you). You can also consider similar solutions based on OrangePi, NanoPi I only determined the minimum system requirements on which the printer works perfectly.

## How do I know if the firmware has loaded and is working?
When the microcontroller is turned on, the red LED on the "brains" lights up, after activating the "clipper" on the single-board computer, the LED on the "brains" stops lighting up (or continues to light up, if you did not specify this in the configuration).

## I want to add additional sensors that were never in the printer, what to do?
You can bring out many contacts from the main gd32f105 brains, but the best solution is to use an additional mcu.
Klipper allows you to connect many different microcontrollers, it all depends on your choice. The most optimal, complete and simple solution is to use the rp2040 (which, according to the new firmware, runs at 200 MHz!), and requires a simple usb connection to connect to klipper.

I also added a few other firmware for mcu, these are stm32f103 and atmega328p. I do not recommend using the firmware based on atmega328p, as it is very stripped down and was intended only for those people who just want to add very useful functionality to the printer from the factory (backlight, fan control).

## Run "printer.cfg"
Here I can't give exact recommendations what your "ideal" and correct configuration should be, it may differ, since my device is not so original. Speed settings, acceleration, extruder steps, everything was adapted to the factory ones from the factory firmware. Just use it as a starter!

```toml
[include fluidd.cfg]

[virtual_sdcard]
path: /home/alarm/printer_data/gcodes
on_error_gcode: CANCEL_PRINT

[mcu]
serial: /dev/ttyS0 # or usb device
baud: 250000 # or 460800
restart_method: command

[printer]
kinematics: cartesian
max_velocity: 300 # test 140
max_accel: 3600 # default 1000
max_z_velocity: 20 # default 5, The default value is 5. Note that the printer's Z-axis rotation speed is heavily limited from the factory. This is normal, but the problem is that even in the slicer, this value is usually set to 15 (while in the configuration, it's 5), and even the Marlin firmware itself always limits the speed during movement, which raises questions (after all, the slicer configuration was designed for this printer, but even its factory settings are ignored by the firmware itself).
max_z_accel: 450 #  default 100
square_corner_velocity: 8.0 # or 4.0/7.0

[stepper_x]
# brain_channel num: 1
step_pin: PB5
dir_pin: !PB6
enable_pin: !PB7
microsteps: 16
rotation_distance: 8 # 200 * 16 / 400.00
endstop_pin: ^!PC11
position_endstop: -4
position_min: -4
position_max: 120
# If you need more than 120, check your configuration. You can get by with 124-125, or even 126... but I've noticed that the maximum value varies depending on the axle, and this is the factory value; for reasons unknown to me, it fluctuates between 1 and 2 or 3. To test, simply increase the maximum value to 126, and then gradually increase it by 1 from 120. If you hear a knocking sound, that's your maximum value. It's best to never exceed or even set the limit at which you'll hear a knocking sound.

homing_speed: 12

[stepper_y]
# brain_channel num: 2
step_pin: PB8
dir_pin: !PB9
enable_pin: !PB4
microsteps: 16
rotation_distance: 8 # 200 * 16 / 400.00
endstop_pin: ^!PC10
position_endstop: -4
position_min: -4
position_max: 120
# If you need more than 120, check your configuration. You can get by with 124-125, or even 126... but I've noticed that the maximum value varies depending on the axle, and this is the factory value; for reasons unknown to me, it fluctuates between 1 and 2 or 3. To test, simply increase the maximum value to 126, and then gradually increase it by 1 from 120. If you hear a knocking sound, that's your maximum value. It's best to never exceed or even set the limit at which you'll hear a knocking sound.

homing_speed: 12

[stepper_z]
# brain_channel num: 3
step_pin: PB3
dir_pin: !PD2
enable_pin: !PC12
microsteps: 16
rotation_distance: 8 # 200 * 16 / 400.00
endstop_pin: ^!PA8
position_endstop: -3.25
position_min: -3.25
position_max: 125.5
homing_speed: 9

[extruder]
# brain_channel num: RJ45
step_pin: PA4
dir_pin: !PA1
enable_pin: !PA0
microsteps: 16
rotation_distance: 34.5572354212 # 200 * 16 / 92.60 for default e-steps 92.60
heater_pin: !PB10
sensor_type: ATC Semitec 104GT-2
sensor_pin: PC5
min_temp: 0
max_temp: 280
control = pid
pid_kp = 36.524
pid_ki = 2.387
pid_kd = 139.704
max_power: 1.0
pwm_cycle_time: 0.1

nozzle_diameter: 0.4
filament_diameter: 1.75
#pressure_advance: 0.05 # only test

[output_pin LED_R]
pin: mcu:PC7
value:0

[output_pin LED_B]
pin: mcu:PC8
value:0

[output_pin GATE_CTRL]
pin: mcu:PB0
value:1

[output_pin MAIN_POWER]
pin: mcu:PF2
value:1

[output_pin STEPPER_POWER]
pin: mcu:PF1
value:1

[heater_bed]
heater_pin: PA7
sensor_pin: PC4
sensor_type: EPCOS 100K B57560G104F
min_temp: 0
max_temp: 85
control: pid
pid_kp: 65.934
pid_ki: 2.730
pid_kd: 398.078
pwm_cycle_time: 0.1
max_power: 1.0

[bed_mesh]
speed: 80
horizontal_move_z: 1
mesh_min: 10, 10
mesh_max: 115, 115
probe_count: 3, 3
algorithm: lagrange
bicubic_tension: 0.2

[bed_mesh default]
version = 1
points =
 	  -0.500000, -0.100000, 0.200000
 	  -0.400000, -0.100000, 0.200000
 	  -0.400000, -0.100000, 0.300000
x_count = 3
y_count = 3
mesh_x_pps = 2
mesh_y_pps = 2
algo = lagrange
tension = 0.2
min_x = 10.0
max_x = 115.0
min_y = 10.0
max_y = 115.0

[firmware_retraction]
retract_length: 5.0 # from the factory
retract_speed: 60 # from the factory
unretract_extra_length: 0.0 # from the factory
unretract_speed: 60 # from the factory

#[firmware_retraction]
#retract_length: 0.6
#retract_speed: 40
#unretract_extra_length: 0.0
#unretract_speed: 20

[gcode_arcs]
#resolution: 1.0

[gcode_macro T0]
gcode:

[gcode_macro M1005]
gcode:

[force_move]
enable_force_move: 1

[homing_override]
gcode:
    # To protect the thermal barrier, nozzle, and platform, we always try to raise the Z-axis, 
    # as it was in the original firmware. Don't leave the printer at home with the home coordinates completely 
    # lost and the Z-axis fully extended!
    {% if 'z' not in printer.toolhead.homed_axes %}
        FORCE_MOVE STEPPER=stepper_z DISTANCE=10 VELOCITY=5
    {% else %}
        {% if printer.toolhead.position.z < 100 %}
            G91
            G1 Z10 F1200
            G90
        {% endif %}
    {% endif %}

    G28 X
    G28 Y
    G28 Z
    
    G1 Z-1 F1200

#[stepper_z2]
# brain_channel num: 5
#step_pin: PC2
#dir_pin: !PC1
#enable_pin: !PC3
#microsteps: 16
#rotation_distance: 8 # 200 * 16 / 400.00
#endstop_pin: ^!PC0
#position_endstop: -3.25
#pposition_min: -3.25
#position_max: 125.5
#homing_speed: 9
```
Don't forget to check the sensors on your device before printing, PID calibration (extruder and bed), manual bed height calibration, ... and only then the print itself.

## Resonance compensation
<a href="../resonances/Readme.md">See</a>

## Can Luban be used? (slicer)
Most likely not, Luban does rollbacks strangely and I don't even know why, no oddities with rollbacks to gcode from Cura or similar slicers were noticed. But for starters, you can try to print test prints on Luban (on large models such oddities are less noticeable).

## Cura (slicer)
<a href="../cura/Readme.md">See</a>

## Klipper machine tweaks
<a href="./Klipper_Machine_Tweaks.md">See</a>

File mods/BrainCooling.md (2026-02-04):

#### Brain cooling (40mm)
This is a more or less simple way to replace one of the fans, namely the fan in the brains with a 40mm fan (as far as I remember), in addition to the model itself, you will probably need a 12V converter (if you use a 12V fan) and a dremel to cut out the original plastic from the brains. Here is a printable model https://www.thingiverse.com/thing:6123116 (I am not the author of this model, it is simply in the public domain, <a href="https://creativecommons.org/licenses/by/4.0/">Creative Commons - Attribution license</a>)

#### Brain cooling (80mm)
<a href="./brain_80mmfan/brain_80mmfan.md">See</a>

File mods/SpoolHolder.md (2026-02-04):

#### Spool holder (3D)
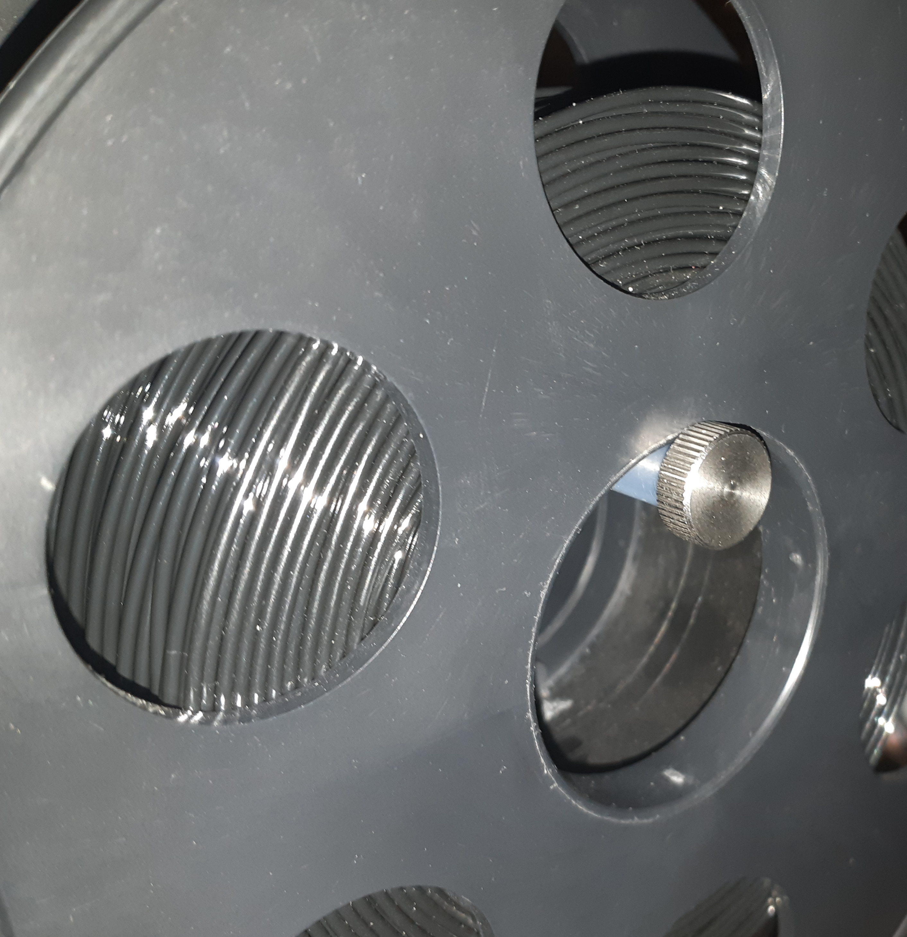
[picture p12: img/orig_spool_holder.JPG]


The original very small spool could be used further in this printer, but I mainly use full-size plastic spools weighing 1 kg and often encounter feed instability during printing due to uneven movement of the spool along the axis, there are also situations when it is necessary to move the printer from place to place and here situations of falling of the plastic spool are not uncommon. I settled on an open solution https://www.thingiverse.com/thing:3413947 (I am not the author of this model, it is just in the public domain, <a href="https://creativecommons.org/licenses/by/4.0/">Creative Commons - Attribution license</a>) it prints perfectly on this printer, holds the spool firmly, rotates easily and adjusts to any spool size, the author provided a full original threaded fixation!

Please note that the use of any Teflon guide tubes in the filament flow negatively affects the final prints, in this printer, due to the incorrect angle of the spool, these flow changes are especially noticeable!
It was also recommended that if you do not use this modification, it is better to position the coil counterclockwise, and if with this modification, then clockwise!

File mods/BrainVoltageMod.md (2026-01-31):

### BrainVoltageMod

#### Disclaimer
I am not responsible for your damaged 3D printers and single board computers, I do not give advice, this information is provided as is, you can use it only at your own risk.

#### Description
This procedure is necessary if you want to replace the original stepper motors with motors requiring higher currents. The image shows a detailed schematic and indicates which resistors should be used instead. I recommend using short, soft silicone wire (if you're installing a resistor or potentiometer on the wire).

<i>I've used this circuit to connect other, more interesting stepper motors (such as one with a 0.9-degree rotation angle) to the extruder. Currently, I have a simple 17HS4401S stepper motor with a 0.9-degree rotation angle, and I replaced the 4.7kΩ resistor with a 13kΩ resistor, increasing the current from ~0.5A to ~1.3A.</i>

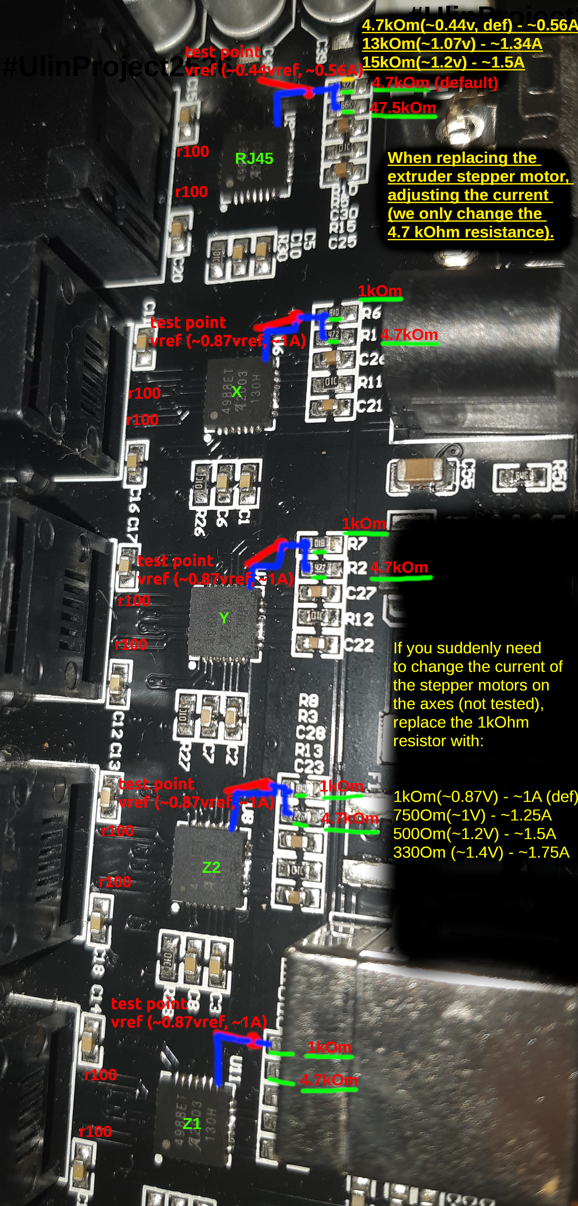
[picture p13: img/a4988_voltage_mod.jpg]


#### Caution!
Stepper motors are connected using a standard twisted cable. This cable may not be suitable for connecting stepper motors with a current greater than 1.1 A! (Even at 1.1 A, you will likely experience a significant voltage drop.)

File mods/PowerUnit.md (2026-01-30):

#### Power unit
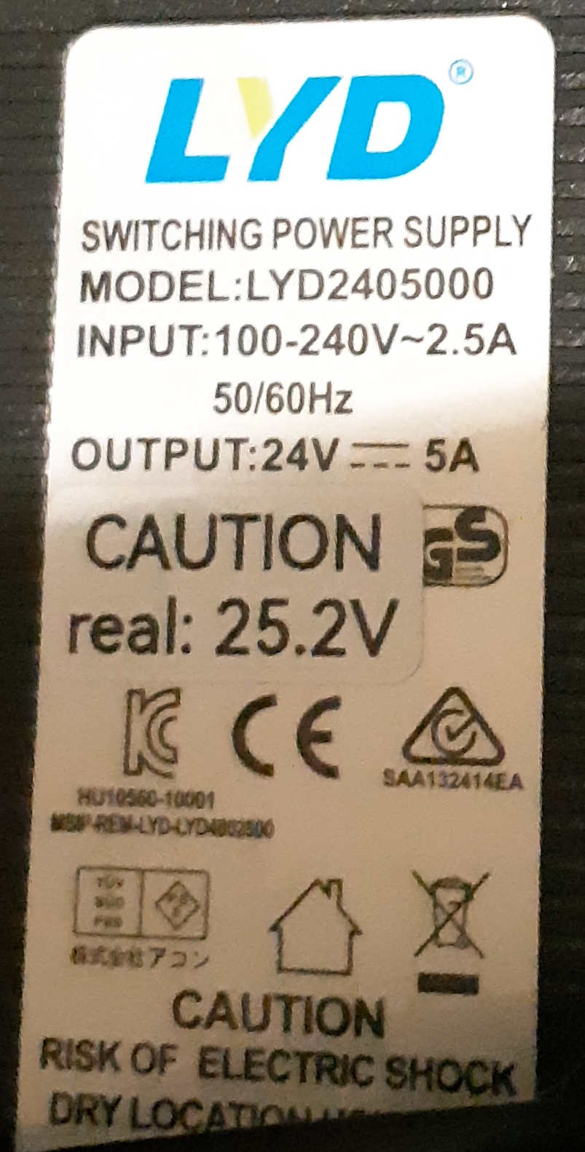
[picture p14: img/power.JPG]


A 24V 5A (120W) power supply is used. The reason for this choice is unclear, but out of the box, it delivered 25.2V. While a 0.2V overhead can be justified to compensate for voltage drop across the wiring, a 1.2V excess is significant and potentially harmful to the electronics, as components like fans and heaters are rated strictly for 24V. My theory is that this was intentional to offset the 1.2V sag that occurs when the hotend and heatbed are heating simultaneously. You can even hear the voltage drop by the change in fan pitch, as they are wired directly to the 24V rail.

Furthermore, this stock PSU is passively cooled and gets quite hot during long prints, though it remains functional.
I happened to have an old Mean Well S-150-24 (24V ~6.5A, 150W) in my spare parts bin. It’s not the most modern choice, but it's reliable. I adjusted it to 24.2V and used double wiring to power the printer. Now, the voltage drop is only 0.2V under full load, which is perfectly acceptable.

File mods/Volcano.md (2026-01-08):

#### Volcano (3D)

At first I wasn't too keen on using the stock hotend but surprisingly it printed very well, an extra hotend was included in the spares and after catching the plastic plug again (but this time due to an Octoprint software bug the filament just popped out) and using the extra hotend I didn't want to go out and buy the original hotend or try to burn and oxidize it, I wanted something new.

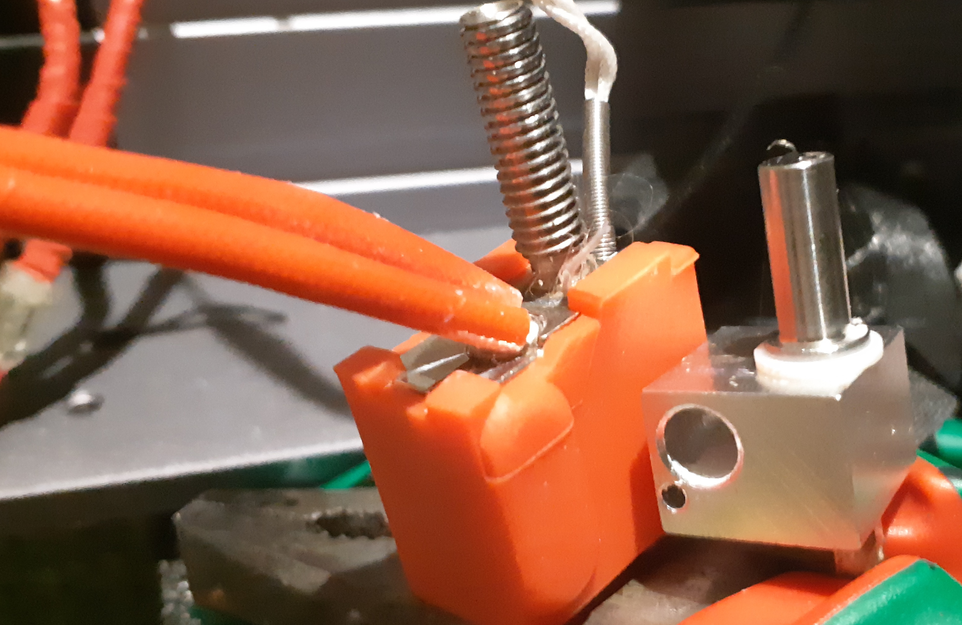
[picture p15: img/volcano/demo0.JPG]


After digging through my spares and finding two Volcano aluminum hotends with a silicone sock, a temperature sensor (already in the sleeve) and a heater from Triangle Lab I started thinking about adapting the stock extruder to the Volcano!

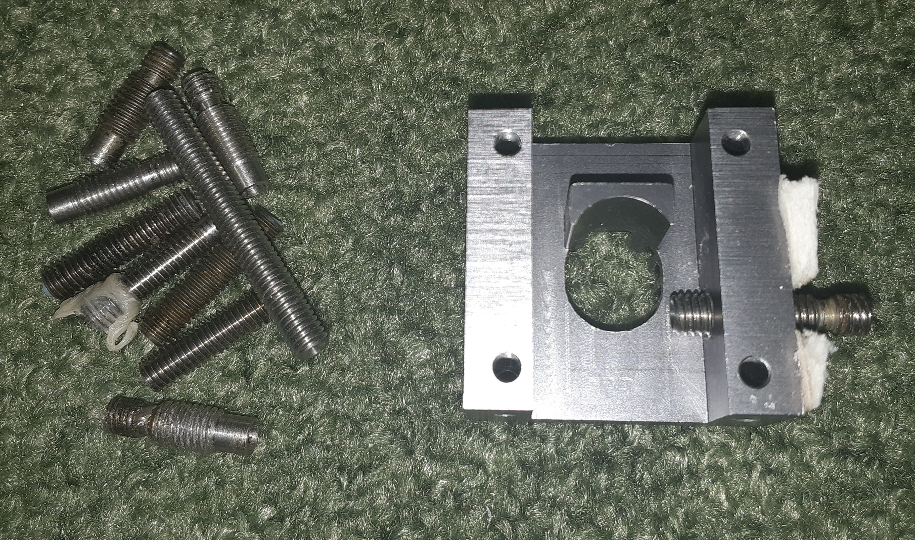
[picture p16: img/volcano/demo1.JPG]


The first thing I ran into was the inability to use the standard bimetal thermal break, thermal breaks are essentially a transition from a large thread diameter to a small one and this hotend was designed with one diameter and no threads along the entire length. And even after cutting the threads in the radiator (while maintaining the ability to use the original thermal blocks), I was able to screw only a bimetallic thermal barrier into the original radiator, and that from the other side. After digging around, I found a thermal barrier with a thread that has the same diameter along its entire length, but is still a thermal barrier. In the future, I will need to order a thermal barrier with half a thread and half without a thread. In general, the diameter could be increased in the original radiator, but I decided to leave the option of using the original block.

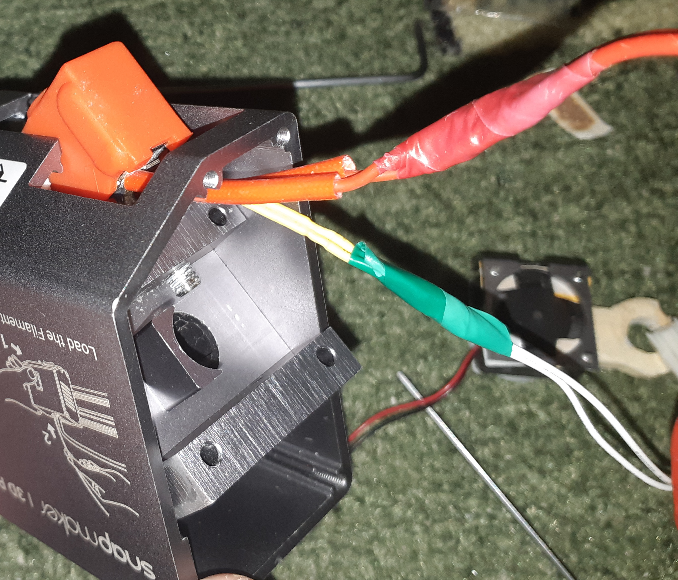
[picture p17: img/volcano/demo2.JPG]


Having measured the distance, I installed the thermal barrier and began to assemble the hotend using fum tape and thread lock. The main difficulty in installing the hotend was the complexity of placement, oddly enough, there was a partition in the extruder head that interfered with the installation of the radiator, and the extruder became several times longer, but the solution was the simplest - slightly grind down the edge of the radiator or install the radiator, but using the space from the other edge of the head.


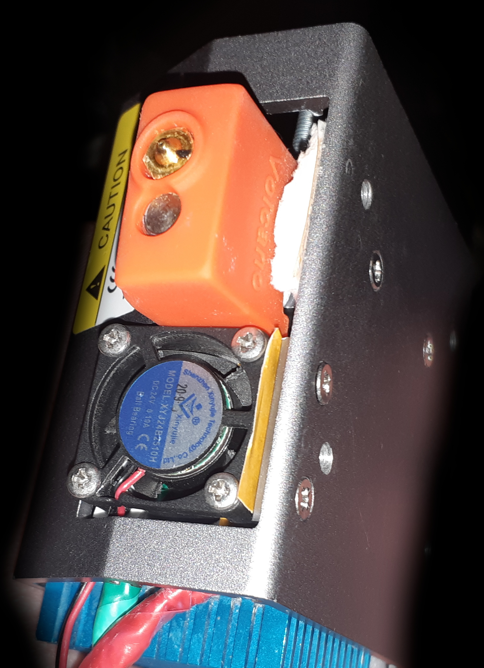
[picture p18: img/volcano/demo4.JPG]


And so, having assembled this strange creation, I started installing and testing it, and my terrible expectations were justified... the extruder simply crashed into the platform, I had to raise the Y-axis to maintain the original length, temporarily putting washers under it and adjusting the height, I determined a convenient size for myself (in the future I will need something made of metal with the right dimensions) for testing.


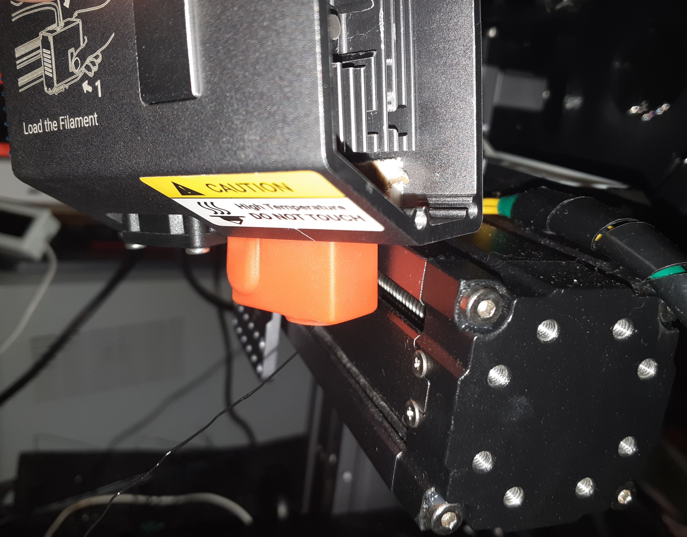
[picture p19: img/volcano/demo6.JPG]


And then I had to set it up for a long time, the extruder became many times longer, I had to make sure that the steps and flow rate settings were correct, I also had to make sure that the temperature sensor readings were correct, since it was not the original one, the firmware supports PID autocalibration, but I was unable to achieve constant readings, and the original PID generally suited me.

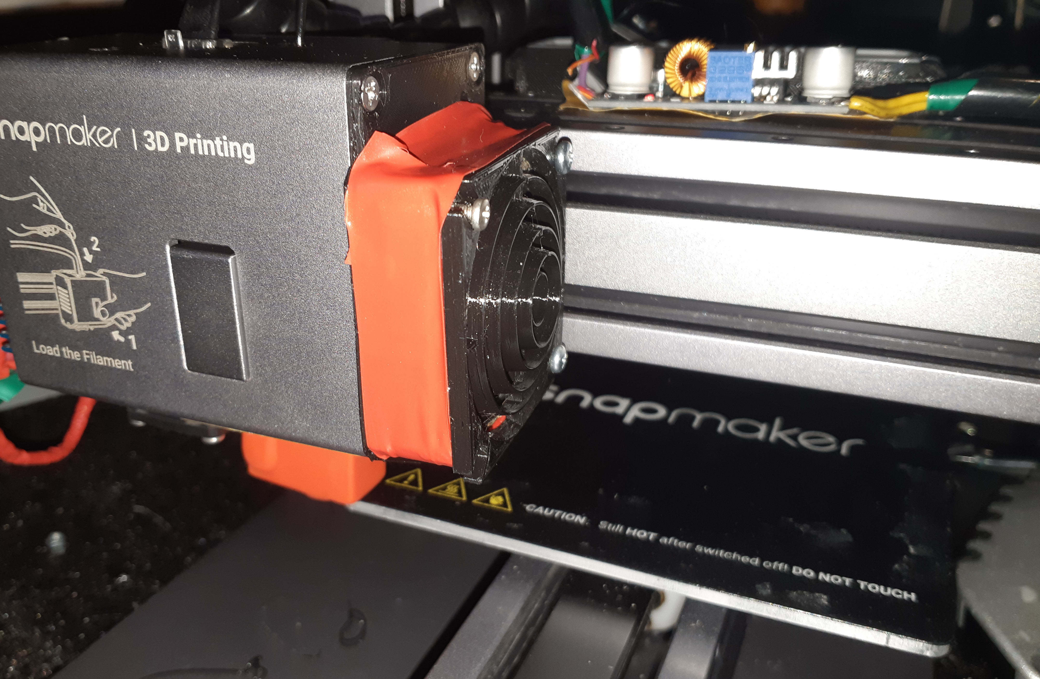
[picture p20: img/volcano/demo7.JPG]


According to the tests, the extruder began to heat up many times longer, and the correctness of the readings was also unclear. Having printed the first test calibration models, I was convinced of the strangeness of the extrusion, if earlier it was necessary to reduce the feed to 98% (with the standard 100%), now according to the tests the feed had to be increased to 101%, which is strange, and the models became worse, and some even better, and the quality of the output plastic filament became many times better. I also had to recalibrate the surface, since the extruder itself is on a screw connection (inaccuracies in parallelism relative to the "bed") and the Y axis was previously increased. After recalibrating the "bed" I managed to lower the fan lower and faced the fact that printing always ended with complete detachment of the model, after a long recalibration of the model it turned out that the standard 205/200 (first layer and final layer) degrees are not enough for printing PLA, I had to increase the temperature to 220 and 217 (at 215 the extruder has a hard time), which gave generally good prints.



#### VolcanoRaiseZ-Axis
To install the Vulcan hotend modification, you need to raise the Z-axis. You can use my <a href="./VolcanoRaiseZ-Axis.stl">model</a>, and it's best printed in PETG (note that my model was adjusted to fit my printer; always check carefully, otherwise the nozzle will hit the platform. If you notice that the height isn't enough, adjust the Z-axis in the model in the slicer!).

## License

These STL model (VolcanoRaiseZ-Axis.stl) are licensed under the **Creative Commons Attribution-NonCommercial 4.0 International (CC BY-NC 4.0)** license.

You are free to:
- Print and use this model for non-commercial purposes
- Modify and adapt the model
- Share derivative works, provided the terms are respected

Under the following terms:
- You must give proper credit to the original creator — **#UlinProject** or **Denis Kotlyarov**
- You may not use the model or its derivatives for commercial purposes without explicit permission

Full license text: [CC BY-NC 4.0 Legal Code](https://creativecommons.org/licenses/by-nc/4.0/legalcode)

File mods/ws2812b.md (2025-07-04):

### ws2812b.stl
Useful <a href="./ws2812b.stl" width="11%">3d model</a> for attaching a small piece of ws2812b tape (5v version) on a PCB to a beam. Lighting control is best done with an additional controller (like rp2040) and a 5v logic level converter.

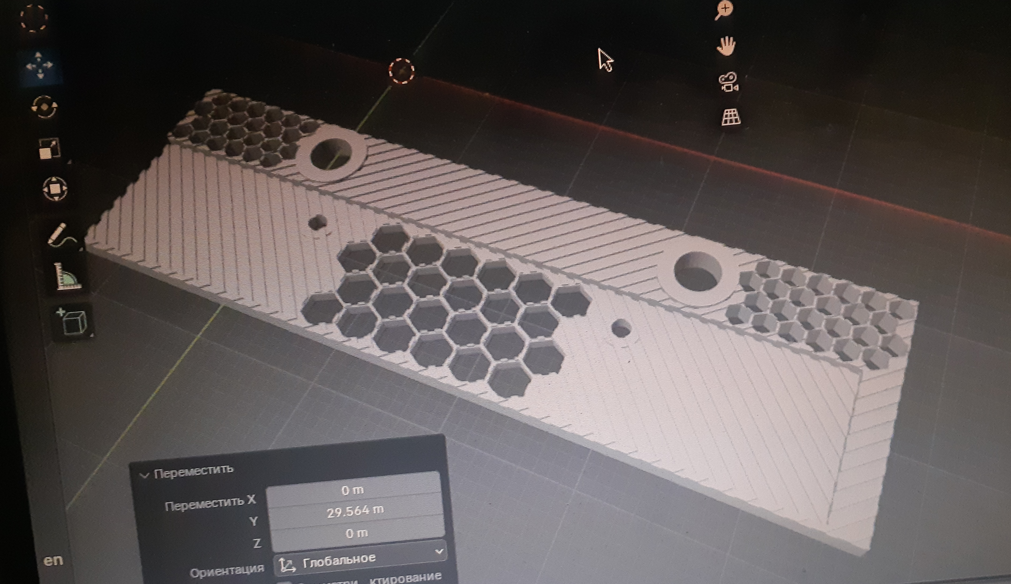
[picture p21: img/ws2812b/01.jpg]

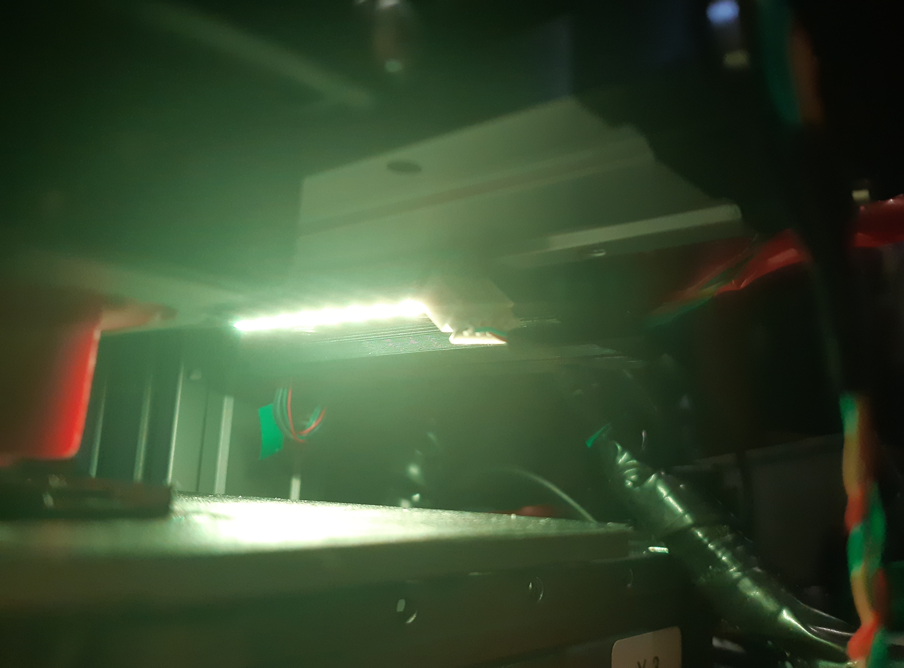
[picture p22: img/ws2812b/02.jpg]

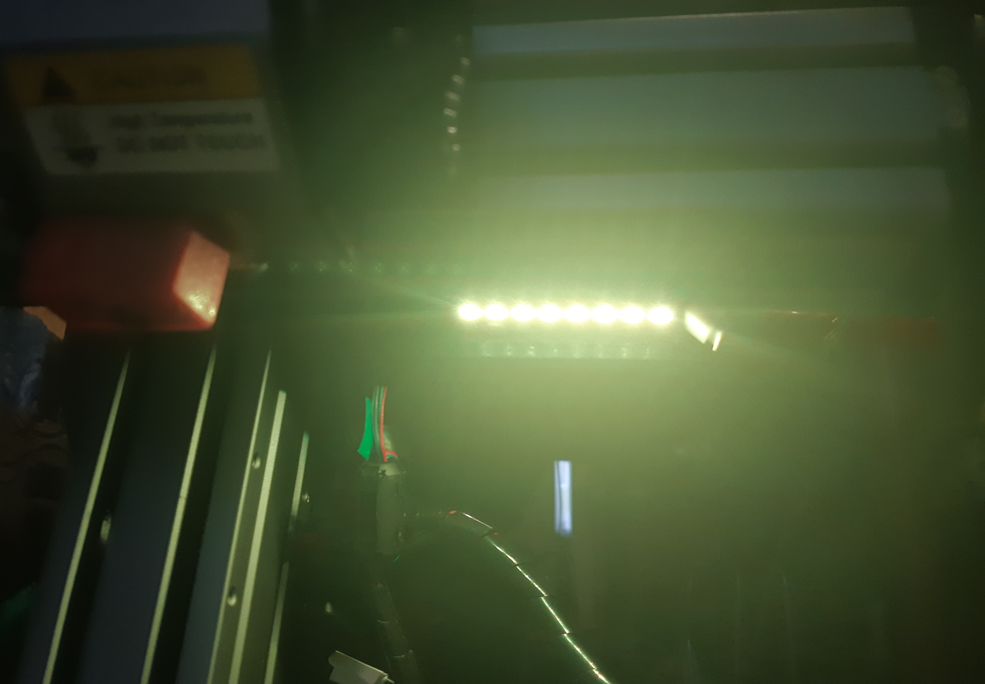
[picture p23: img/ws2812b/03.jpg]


## License

This <a href="./ws2812b.stl" width="11%">STL model</a> is released under the **Creative Commons Attribution-NonCommercial 4.0 International (CC BY-NC 4.0)** license.

You are free to:
- Print and use this model for non-commercial purposes
- Modify and adapt the model
- Share derivative works, provided the terms are respected

Under the following terms:
- You must give proper credit to the original creator — **#UlinProject** or **Denis Kotlyarov**
- You may not use the model or its derivatives for commercial purposes without explicit permission

Full license text: [CC BY-NC 4.0 Legal Code](https://creativecommons.org/licenses/by-nc/4.0/legalcode)

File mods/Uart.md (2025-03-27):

### UART

#### Disclaimer
I am not responsible for your damaged 3D printers and single board computers, I do not give advice, this information is provided as is, you can use it only at your own risk.

#### About the factory firmware
Very weak (115200 baud) feedback and high latency do not give good prints. Eliminating the latency that occurs on USB allows octoprint to work better and print better. This printer prints better from a USB stick.

The printing problem on the factory firmware is more or less solved by the firmware "32Base_2_11_01Demo250000BOUD.Bin". Starting with "32Base_2_11_04Demo500000BOUDAndMoreSerialMods.bin" the problem is completely fixed on firmware with active "buffer buddy" (plugin on octoprint) and can be used with USB key, but 500000 baud rate may not suit everyone, and you can use simpler without special edits "32Base_2_11_01Demo250000BOUD.Bin" at 250000 baud.

#### Direct UART connection to SBC (single board computer)


It is possible to connect the microcontroller and SBC directly, eliminating the influence of USB connection. The photo shows the contacts that need to be soldered to the wires to use UART of SBC and microcontroller directly, without converting to USB and back. After soldering the contacts I recommend removing the ch340g chip (but you will lose USB support)

#### Things to remember when using Raspberry Pi single board computers with direct UART connection
1. Enable uart with "enable_uart=1" in config.txt
2. Disable system services
```
sudo systemctl stop serial-getty@ttyS0.service
sudo systemctl disable serial-getty@ttyS0.service

sudo systemctl stop serial-getty@ttyAMA0.service
sudo systemctl disable serial-getty@ttyAMA0.service
```
3. Do not use mini UART (/dev/ttyS0), it is better to disable it, it will only hinder you (you will lose the ability to use bluetooth). When using this interface, connection latency is not constant, performance is variable
add to config.txt
```
dtoverlay=pi3-disable-bt
dtoverlay=disable-bt
```
Now you can specify /dev/ttyAMA0 in octoprint or klipper config.

4. <b>(Optional, may not work for everyone)</b> You can increase the UART clock speed and get a theoretical maximum of ~4 Mbps over UART
Add to config.txt:
```
init_uart_clock=64000000
```

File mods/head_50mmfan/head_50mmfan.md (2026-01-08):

### head_50mmfan

My cover design allows for the installation of a 50mm fan with minimal impact on the thermal block itself. Please note that due to the insufficient height, you will need to weld the mounting nuts to the plastic and align them so the cover closes tightly. Only then can you secure the fan with all four screws, or use just two screws without this procedure.

Make sure you don't blow directly onto the thermal block. If air leaks in, insulate it. Air should flow freely through the heatsink and the top of the thermal barrier.

Theoretically, this cover can be installed on other modules (for CNC or laser cutting), but this has not been tested.

## Files

- <a href="./body.stl">body.stl</a> - lid.
- <a href="./limitation.stl">limitation.stl</a> - limiting the air supply to avoid affecting the model during printing..

## License

These STL models (body.stl, limitation.stl) are licensed under the **Creative Commons Attribution-NonCommercial 4.0 International (CC BY-NC 4.0)** license.

You are free to:
- Print and use this model for non-commercial purposes
- Modify and adapt the model
- Share derivative works, provided the terms are respected

Under the following terms:
- You must give proper credit to the original creator — **#UlinProject** or **Denis Kotlyarov**
- You may not use the model or its derivatives for commercial purposes without explicit permission

Full license text: [CC BY-NC 4.0 Legal Code](https://creativecommons.org/licenses/by-nc/4.0/legalcode)

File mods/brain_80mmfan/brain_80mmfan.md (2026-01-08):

### brain_80mmfan

My alternative to cooling the brains of this printer, made specifically for 80mm fans, turns out to be an absolutely silent system and quite productive.

## Files

- <a href="./body.stl">body.stl</a>
- <a href="./out.stl">out.stl</a> - protective cover for the fan.

## License

These STL models (body.stl, out.stl) are licensed under the **Creative Commons Attribution-NonCommercial 4.0 International (CC BY-NC 4.0)** license.

You are free to:
- Print and use this model for non-commercial purposes
- Modify and adapt the model
- Share derivative works, provided the terms are respected

Under the following terms:
- You must give proper credit to the original creator — **#UlinProject** or **Denis Kotlyarov**
- You may not use the model or its derivatives for commercial purposes without explicit permission

Full license text: [CC BY-NC 4.0 Legal Code](https://creativecommons.org/licenses/by-nc/4.0/legalcode)

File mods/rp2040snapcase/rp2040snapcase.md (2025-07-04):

### rp2040snapcase

Addition of a miniature rp2040 microcontroller for interaction and control of additional functions via klipper firmware. The case itself is equipped with the possibility of further expansion and attachment to the beam, as well as an additional case for modifications. The screws that attach the case to the beam can be either countersunk or standard (but then they will be outside the cover). The parts can be printed on the same printer.

#### # 1A

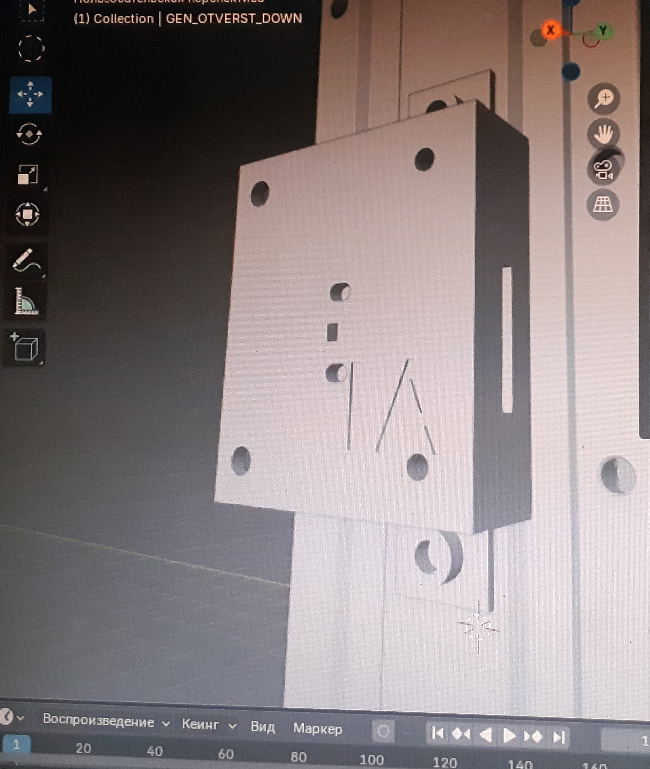
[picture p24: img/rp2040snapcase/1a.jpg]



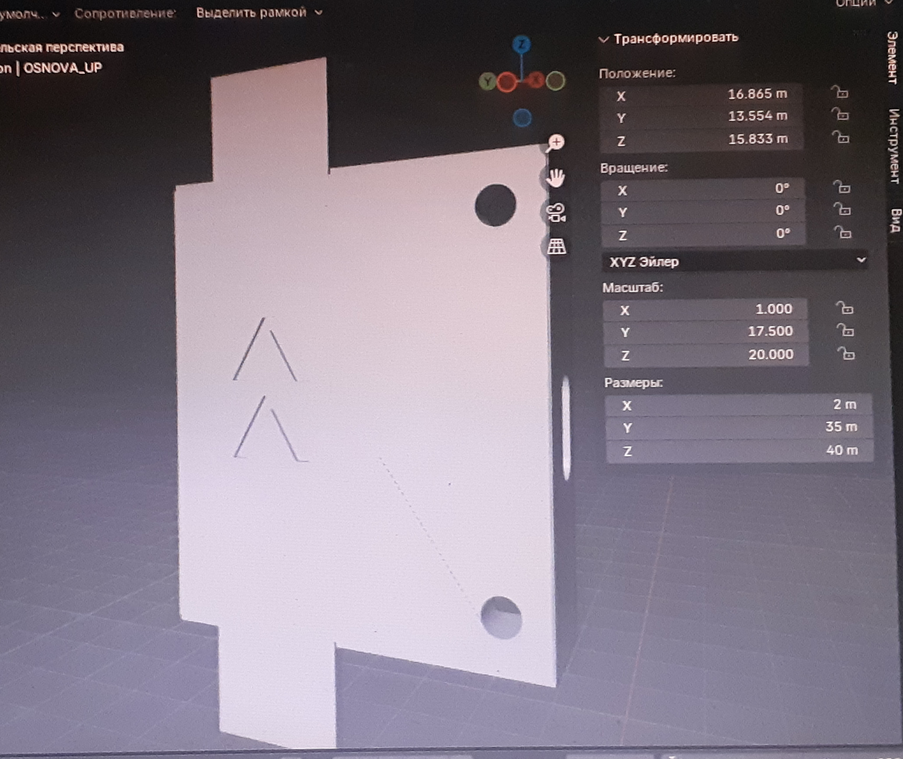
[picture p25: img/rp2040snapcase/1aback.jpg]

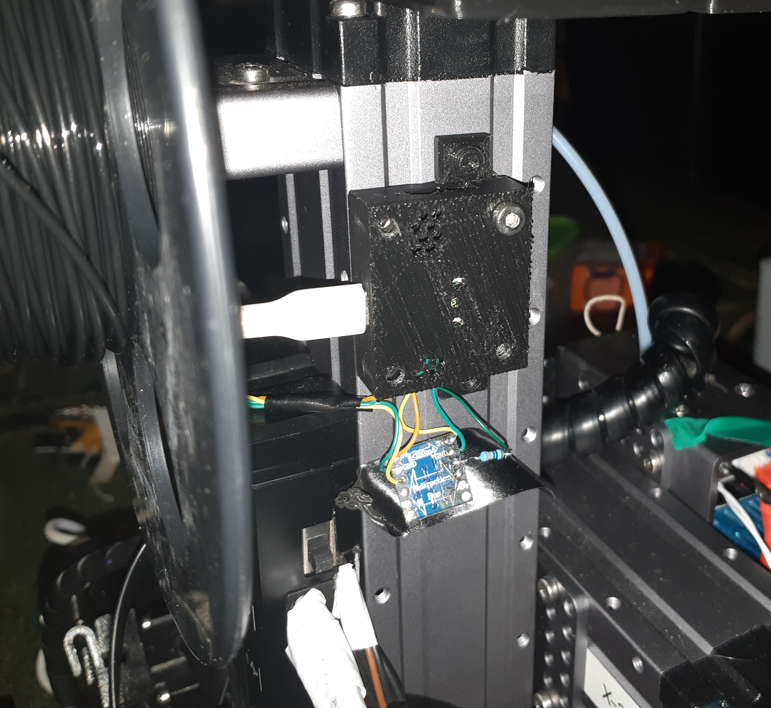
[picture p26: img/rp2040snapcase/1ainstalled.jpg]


#### # 2A

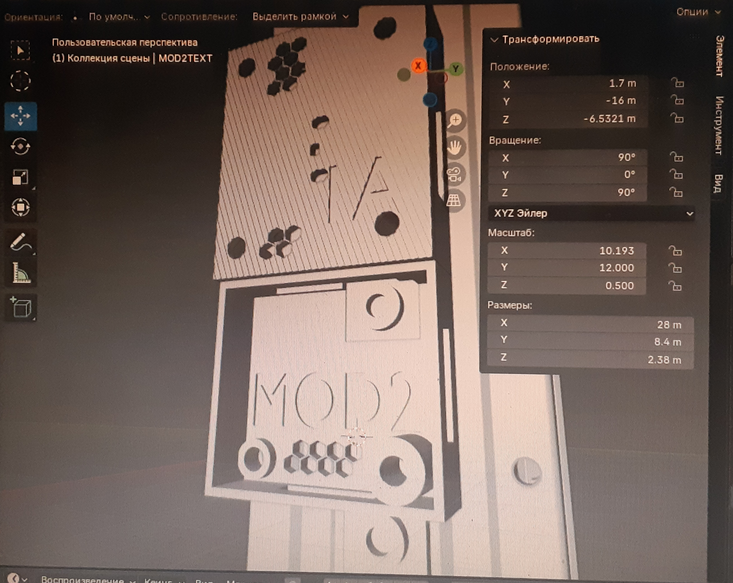
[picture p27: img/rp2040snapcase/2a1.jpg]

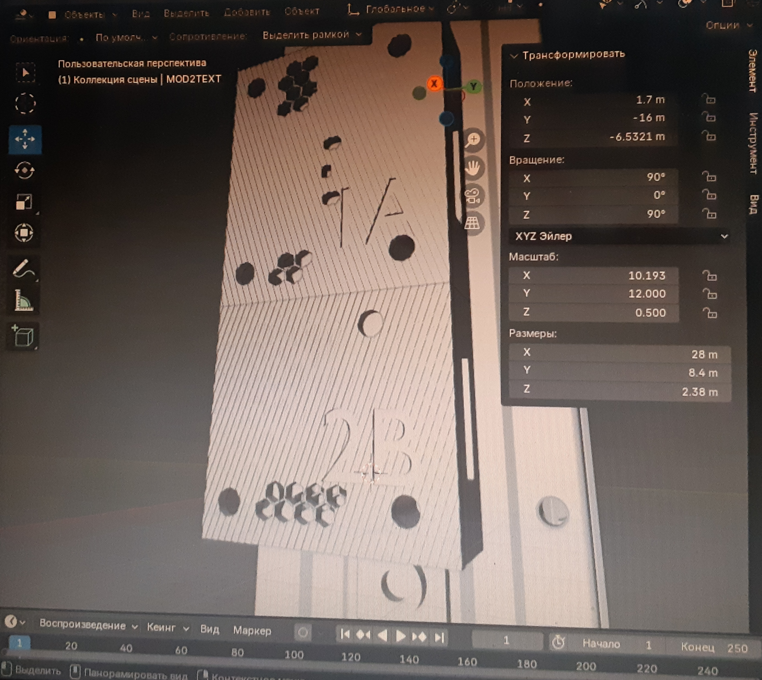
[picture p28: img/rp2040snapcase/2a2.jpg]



## Files

- <a href="./MCU_BOTTOM.stl">MCU_BOTTOM.stl</a> - the housing in which the microcontroller is installed.
- <a href="./MCU_TOP.stl">MCU_TOP.stl</a> - the top cover closes the housing in which the microcontroller is located.
- <a href="./MOD2_BOTTOM.stl">MOD2_BOTTOM.stl</a> - a housing that can be attached to the main body and accommodate additional modifications
- <a href="./MOD2_TOP.stl">MOD2_TOP.stl</a> - the cover closing the additional housing

## License

These STL models (MCU_BOTTOM.stl, MCU_TOP.stl, MOD2_BOTTOM.stl, MOD2_TOP.stl) are licensed under the **Creative Commons Attribution-NonCommercial 4.0 International (CC BY-NC 4.0)** license.

You are free to:
- Print and use this model for non-commercial purposes
- Modify and adapt the model
- Share derivative works, provided the terms are respected

Under the following terms:
- You must give proper credit to the original creator — **#UlinProject** or **Denis Kotlyarov**
- You may not use the model or its derivatives for commercial purposes without explicit permission

Full license text: [CC BY-NC 4.0 Legal Code](https://creativecommons.org/licenses/by-nc/4.0/legalcode)

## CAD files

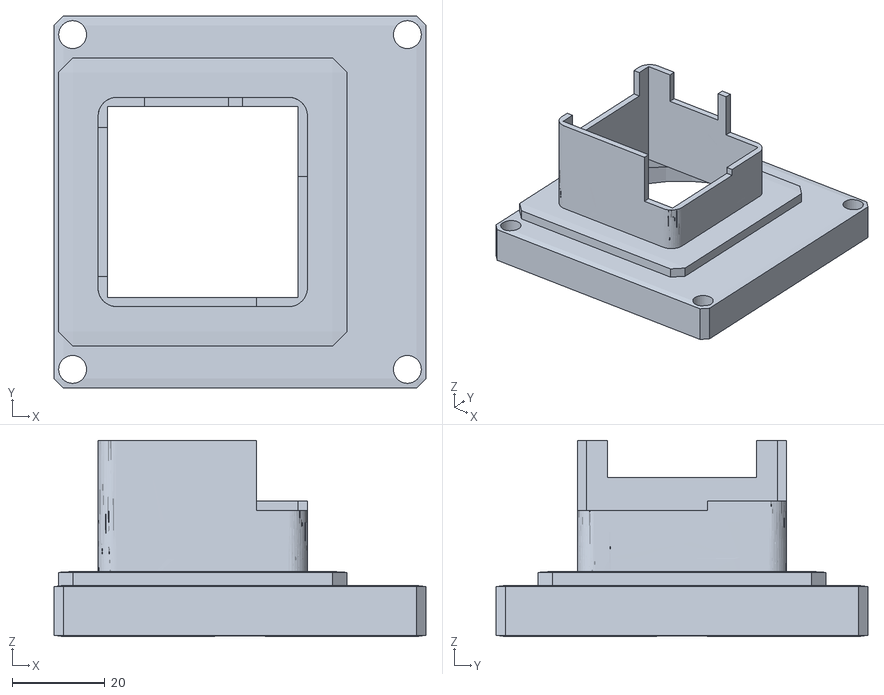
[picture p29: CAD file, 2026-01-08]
mods/brain_80mmfan/body.stl
80.0 x 80.0 x 42.2

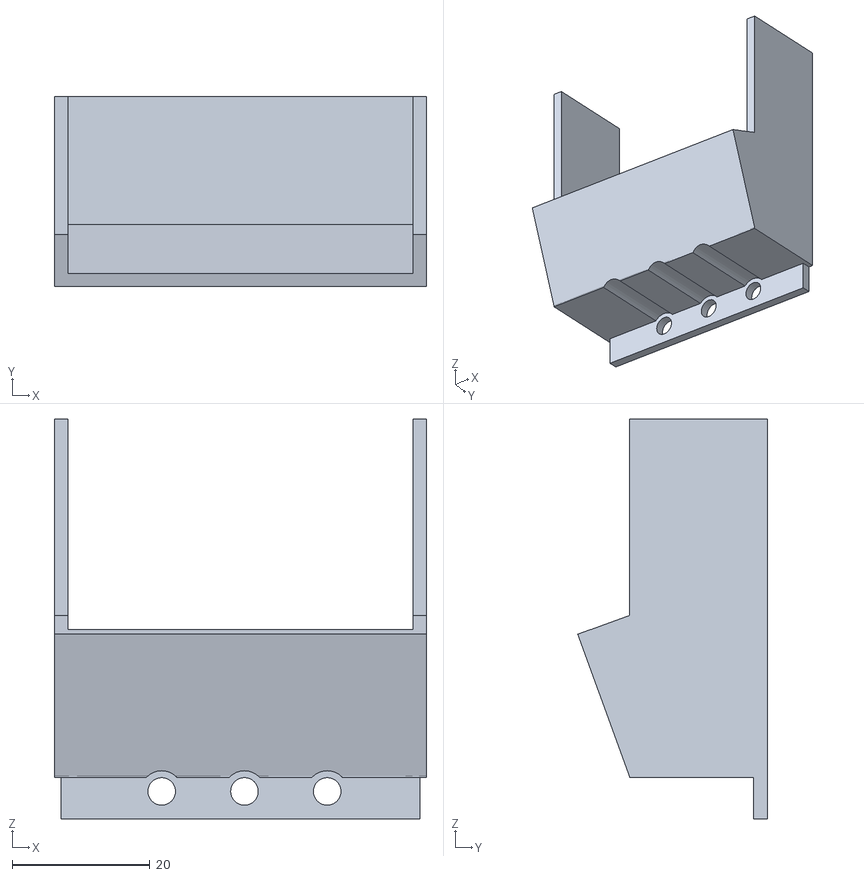
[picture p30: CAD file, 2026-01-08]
mods/head_50mmfan/limitation.stl
54.0 x 27.5 x 58.0

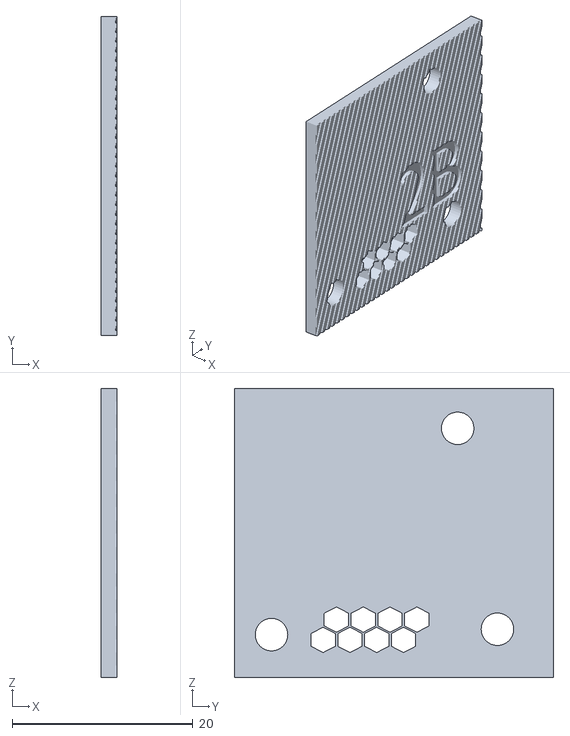
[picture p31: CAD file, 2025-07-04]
mods/rp2040snapcase/MOD2_TOP.stl
1.80 x 35.3 x 32.0

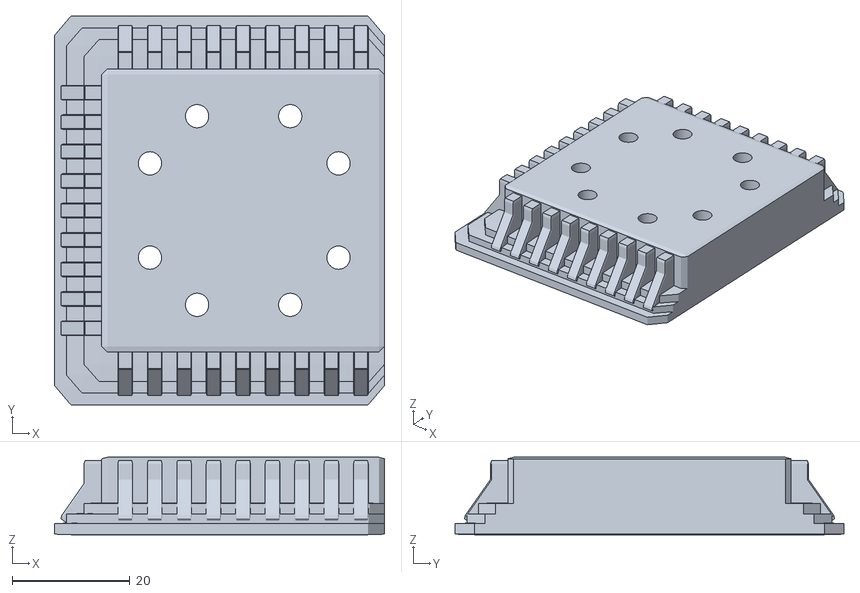
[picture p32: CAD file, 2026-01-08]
mods/VolcanoRaiseZ-Axis.stl
56.0 x 66.0 x 13.2

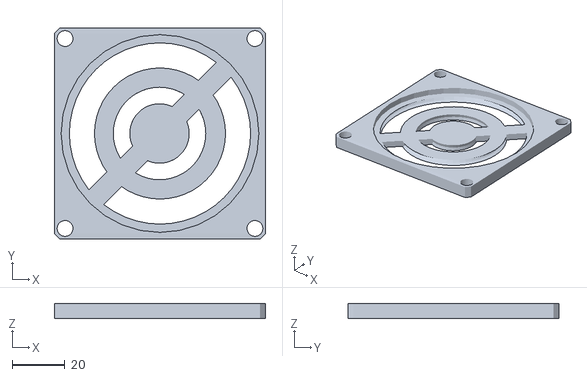
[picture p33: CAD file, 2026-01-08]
mods/brain_80mmfan/out.stl
80.0 x 80.0 x 5.80

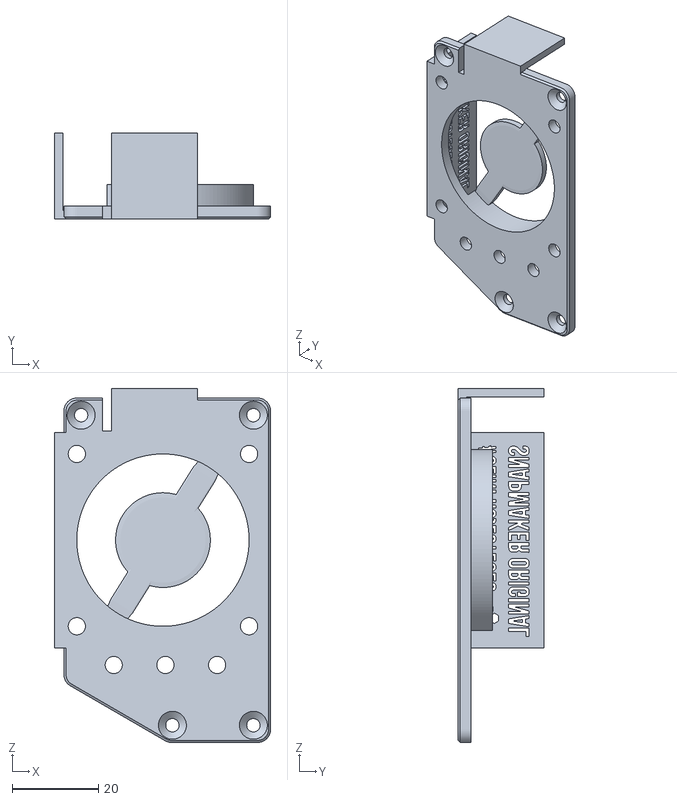
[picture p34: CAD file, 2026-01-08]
mods/head_50mmfan/body.stl
50.2 x 20.0 x 82.2

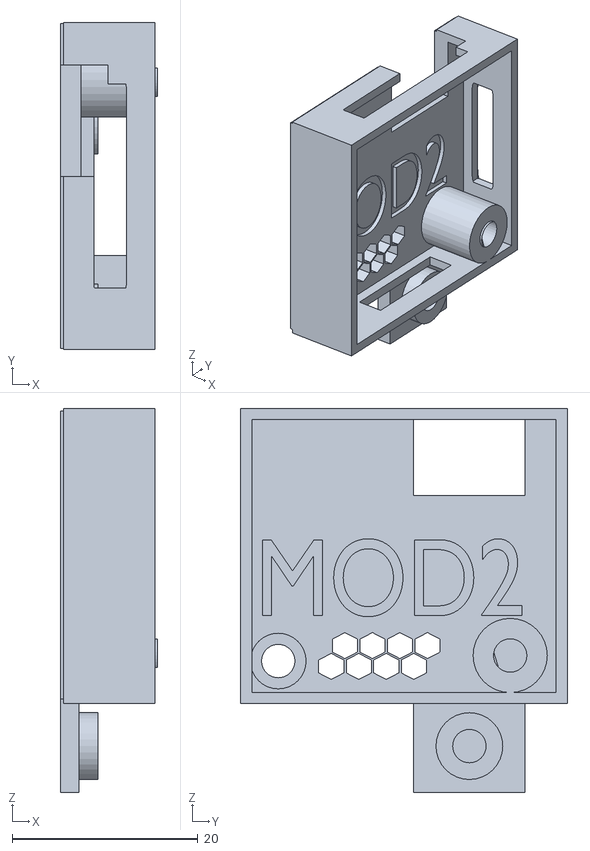
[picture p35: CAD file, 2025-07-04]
mods/rp2040snapcase/MOD2_BOTTOM.stl
10.5 x 35.2 x 41.4

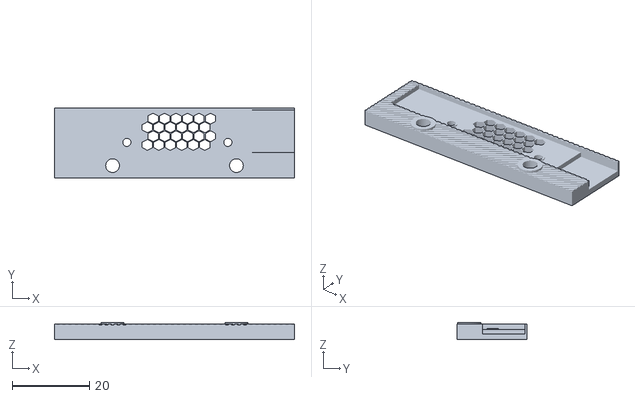
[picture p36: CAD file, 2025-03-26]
mods/ws2812b.stl
62.0 x 18.0 x 4.50

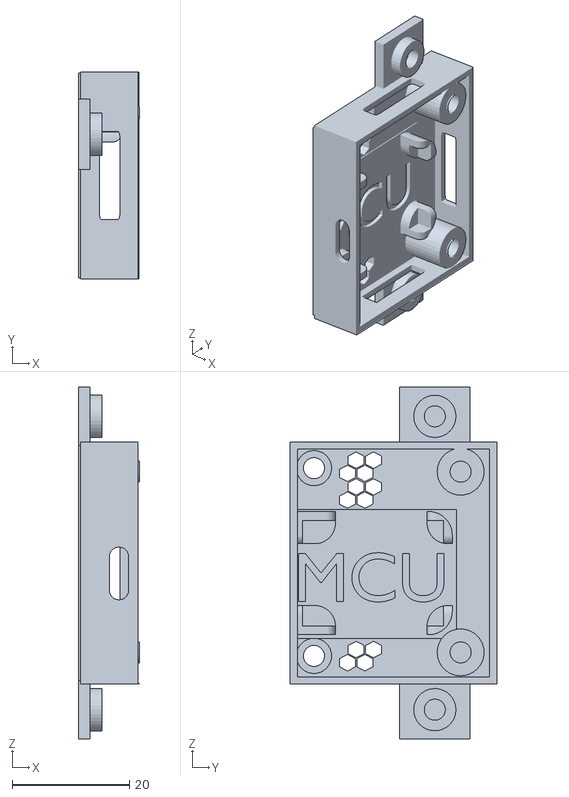
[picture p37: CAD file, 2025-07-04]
mods/rp2040snapcase/MCU_BOTTOM.stl
10.5 x 35.2 x 60.0

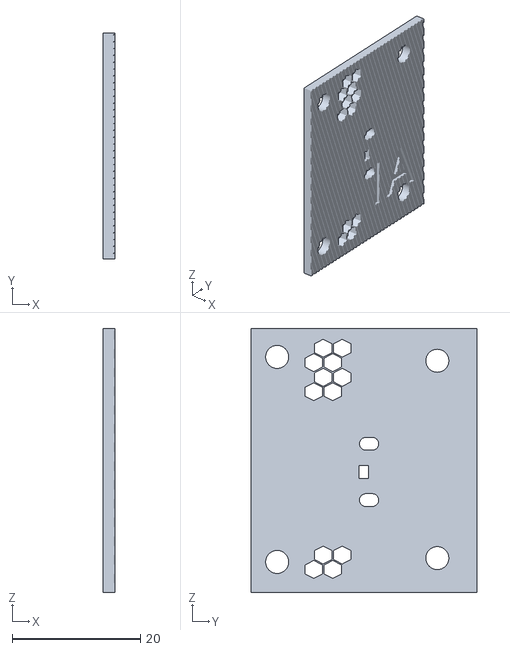
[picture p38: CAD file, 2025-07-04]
mods/rp2040snapcase/MCU_TOP.stl
1.80 x 35.3 x 41.2

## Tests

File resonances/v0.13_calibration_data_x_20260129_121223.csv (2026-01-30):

freq | psd_x | psd_y | psd_z | psd_xyz | zv(126.6) | mzv(130.0) | ei(149.8) | 2hump_ei(145.6) | 3hump_ei(149.8)
0.0 | 0.000e+00 | 0.000e+00 | 0.000e+00 | 0.000e+00 | 1.000 | 1.000 | 1.000 | 1.000 | 1.000
1.6 | 1.716e-11 | 2.722e-13 | 6.139e-14 | 1.749e-11 | 0.998 | 0.997 | 0.997 | 0.995 | 0.993
3.2 | 5.627e-01 | 2.490e-02 | 2.704e-03 | 5.903e-01 | 0.996 | 0.994 | 0.993 | 0.989 | 0.986
4.7 | 3.110e+01 | 2.519e+00 | 3.582e-01 | 3.398e+01 | 0.993 | 0.991 | 0.989 | 0.982 | 0.976
6.3 | 1.132e+02 | 1.265e+01 | 3.918e+00 | 1.298e+02 | 0.990 | 0.987 | 0.984 | 0.974 | 0.965
7.9 | 1.456e+02 | 2.827e+01 | 8.208e+00 | 1.821e+02 | 0.987 | 0.982 | 0.979 | 0.965 | 0.953
9.5 | 2.439e+02 | 3.595e+01 | 7.711e+00 | 2.876e+02 | 0.983 | 0.977 | 0.973 | 0.956 | 0.939
11.1 | 2.988e+02 | 3.290e+01 | 9.137e+00 | 3.408e+02 | 0.979 | 0.972 | 0.966 | 0.945 | 0.925
12.6 | 3.339e+02 | 3.251e+01 | 1.157e+01 | 3.780e+02 | 0.975 | 0.966 | 0.959 | 0.933 | 0.908
14.2 | 3.915e+02 | 2.933e+01 | 1.679e+01 | 4.376e+02 | 0.970 | 0.960 | 0.952 | 0.921 | 0.891
15.8 | 4.740e+02 | 2.767e+01 | 2.845e+01 | 5.302e+02 | 0.965 | 0.953 | 0.944 | 0.908 | 0.873
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

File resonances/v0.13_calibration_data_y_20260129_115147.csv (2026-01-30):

freq | psd_x | psd_y | psd_z | psd_xyz | zv(129.2) | mzv(115.6) | ei(149.8) | 2hump_ei(138.2) | 3hump_ei(125.0)
0.0 | 0.000e+00 | 0.000e+00 | 0.000e+00 | 0.000e+00 | 1.000 | 1.000 | 1.000 | 1.000 | 1.000
1.6 | 2.818e-13 | 1.502e-11 | 1.678e-13 | 1.547e-11 | 0.998 | 0.997 | 0.997 | 0.995 | 0.992
3.2 | 3.277e-02 | 5.140e-01 | 9.172e-03 | 5.560e-01 | 0.996 | 0.993 | 0.993 | 0.988 | 0.982
4.7 | 3.918e+00 | 2.428e+01 | 6.232e-01 | 2.882e+01 | 0.993 | 0.989 | 0.989 | 0.981 | 0.970
6.3 | 1.908e+01 | 8.875e+01 | 3.585e+00 | 1.114e+02 | 0.990 | 0.984 | 0.984 | 0.972 | 0.956
7.9 | 3.511e+01 | 1.564e+02 | 6.920e+00 | 1.984e+02 | 0.987 | 0.979 | 0.979 | 0.963 | 0.939
9.5 | 4.843e+01 | 2.486e+02 | 7.291e+00 | 3.044e+02 | 0.984 | 0.973 | 0.973 | 0.952 | 0.922
11.1 | 4.782e+01 | 2.990e+02 | 6.538e+00 | 3.534e+02 | 0.980 | 0.967 | 0.966 | 0.941 | 0.902
12.6 | 4.320e+01 | 3.113e+02 | 5.750e+00 | 3.602e+02 | 0.975 | 0.960 | 0.959 | 0.928 | 0.880
14.2 | 3.841e+01 | 3.373e+02 | 4.597e+00 | 3.803e+02 | 0.971 | 0.952 | 0.952 | 0.914 | 0.858
15.8 | 3.404e+01 | 3.800e+02 | 4.777e+00 | 4.188e+02 | 0.966 | 0.944 | 0.944 | 0.900 | 0.833
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

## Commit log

2025-03-14 1. Add starter cura profile 2. Add new klipper firmware (921600 support!) 3. Add demo resonances map
    [demo_01_def_resonances_y_20250314_135635.csv, demo_01_volcano_resonances_x_20250314_155812.csv]
2025-03-26 1. Add ws2812b mods 2. Add new klipper firmware 3. Optimize all images
    [ws2812b.stl]
2025-03-26 1. Optimize klipper bin files 1. Add firmware for custom klipper mcu
2025-07-04 feat: add pictures showing the utility model `ws2812b.stl` in action
2025-07-04 feat: add `rp2040snapcase` models
    [MCU_BOTTOM.stl, MCU_TOP.stl, MOD2_BOTTOM.stl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]
2026-01-08 refactor: add a klipper-specific version
2026-01-08 firmware: Add the latest firmware version of Klipper 0.13.0
2026-01-08 add: brain_80mmfan.stl mods
    [body.stl, out.stl]
2026-01-08 add: VolcanoRaiseZ-Axis.stl
    [VolcanoRaiseZ-Axis.stl]
2026-01-08 add: head_50mmfan.stl
    [body.stl, limitation.stl]
2026-01-11 fix: laser.JPG
2026-01-30 files: add new resonances for the 3dmachine
    [v0.13_calibration_data_x_20260129_121223.csv, v0.13_calibration_data_y_20260129_115147.csv]
2026-01-30 fix: make the old demo resonances more specific so that the differences between versions are noticeable
    [v.0.12_demo_01_def_resonances_y_20250314_135635.csv, v.0.12_demo_01_volcano_resonances_x_20250314_155812.csv]
2026-01-31 feat: add voltage mod for a4988 drivers
